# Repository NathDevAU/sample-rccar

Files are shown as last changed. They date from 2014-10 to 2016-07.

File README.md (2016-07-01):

Windows Powered RC Car
===================
---------
Content
-------------

- [Components](#Components)
- [Hooking up Components](#hooking-up-components)
- [Run it!](#run-it!)
- [The Code](#the-code)
- [USB HID Controller Code](#usb-hid-controller-code)
- [Winsock UDP](#winsock-udp)

###Components
- Intel Galileo running Windows off an SD Card
- 5V DC Power Supply (either a wall-powered supply, or a battery pack like [this](http://www.adafruit.com/products/1566) one.)
- A L298N Motor Driver Board ( We've used [this](http://www.ebay.com/itm/like/131207525759?lpid=82) one )
- HID Compliant Controller/Gamepad (We've used an old NES Controller converted to be a HID Device, you can get one [here](http://www.thinkgeek.com/product/1b4c/)
- Microusb Male to USB Female Adapter Cable
- Ethernet Cable
- 4 AA Batteries (or as many batteries as your RC Car needs)
- An RC Car (We've used a Maisito Dune Rover) 
- Male-Female Breadboard Wires

Optional:
- Laptop running Windows & the Remote RC Car Control Application
- Xbox 360 controller for Windows

###Hooking Up Components
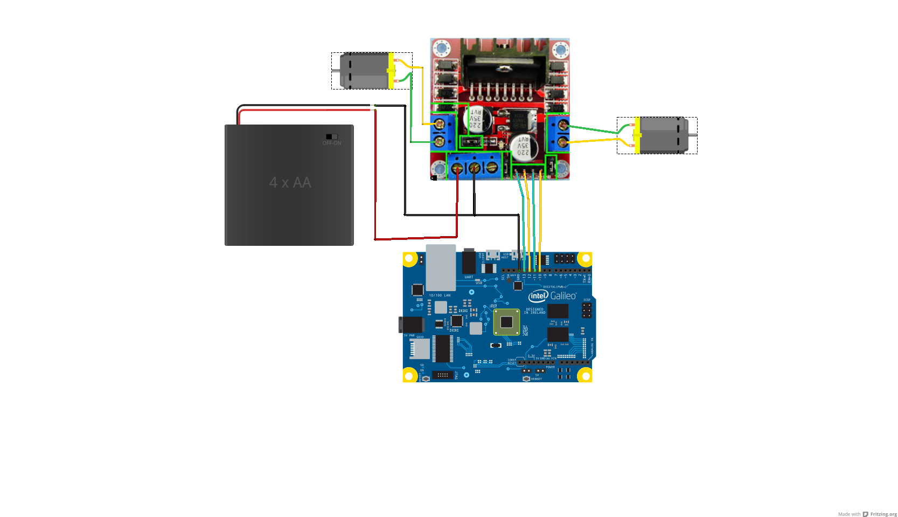
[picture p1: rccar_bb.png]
RC Car


1. Carefully disassemble your purchased RC Car. Specifically, you want to remove the model chassis so you can get at the controller board.

2. You should be able to clearly see 4 wires (two for each motor, assuming a 2 motor RC Car), and 2 more wires from the battery pack, connected to a PCB which contains the controller for the RC Car.

3. Carefully snip away all the leads connected to that PCB. Make sure you know which wire is connected to what part of your RC Car. 

4. Remove the PCB, in it's place, put the L298N Motor Driver Board.

5. Wire up the motor driver board as follows:
>- Connect the +'ve and -'ve leads of one motor to "Output 1" and "Output 2" of the L298N board.
>- Similarily, connect the +'ve and -'ve leads of the other motor to "Output 3" and "Output 4" of the L298N Board.
>- Connect the Battery Pack ground line to the ground input of the L298N Board.
>- Connect the Ground output of the Galileo to the L298N Board Ground input (we want to tie together the grounds of the Galileo and the RC Car)
>- Connect the Battery Pack power line to the +12V input of the L298N Board (don't worry if your battery pack puts out less than 12V)
>- Connect Galileo GPIO pins 13,12,11,10 to Inputs 1-4 of the L298N Board 

**Note: Depending on how you've wired everything up, you may need to play around with the order that you connect these wires to have the controls inverted/regular. In any case, the first motor will be controlled by the inputs 1 and 2, and the second by 3 and 4. To turn on a motor, one of each pair should be high (+5V) and the other low (0V). The motor's direction may be the opposite of what you expect depending on how you've wired it up.

Finally, using the USB adapter cable, plug the NES Controller into the Galileo's USB Host port, and power on the Galileo (make sure the RC Car is turned off until the Galileo is completely booted up and the controller application is running).

###Run it!
Using Visual Studio or Telnet, deploy and run the eCar application. This application runs two threads, one waiting for commands over UDP from a host machine, and the other waiting for local commands from a HID Controller. When commands are received, it drives the GPIO outputs which should drive the motors through the L298N board. 

Once the application has started running on the Galileo, turn on the RC Car and try driving it with the NES controller. With any luck, it should be working just fine! If not, check your wiring as discussed in the Note above.

If you're also using the network-control companion application, you can press "Select" on the NES controller to switch the control mode from local control, to remote from a PC control.

###The Code

There are several files in this project, the purpose of each is listed below.

- Main.cpp
- Controller.cpp and .h
- Communicator.cpp and .h
- Command.h
- nesmapping.h
- stdafx.h

**_Main_**
- The main function that initializes the Galileo pins, and listens to UDP and HID commands to drive the RC Car

**_Controller_**
- Wraps the HID Device communication to talk to the NES Controller

**_Communicator_**
- Wraps the UDP communication done using Winsock

**_Command_**
- An enum representing different commands for the RC Car, used to translate UDP commands

**_nesmapping_**
- Holds the mappings between the NES buttons and their HID identifiers

**_stdafx_**
- Houses all of the external includes for the project

###USB HID Controller Code
Using Windows on Devices gives you access to rich software features that just aren't available on other, similar platforms. One example is full USB support, and several class drivers that are built into the operating system.

For this project, we've used a HID Compliant Gamepad device to drive the input of the RC Car. Take a look at 

**_Controller.h_** and **_Controller.cpp_** to see how to access a HID Device. **_nesmapping.h_** contains the mappings between the HID value and button identifiers with the physical buttons. These need to be determined either from your device's datasheet, or experimentally by writing a program that outputs the button value (see getButtonInput in Controller.cpp for how to read button usages). 

In general, reading from a HID device has XXX main steps, in brackets is the function and line number in which  this step is performed in **_Controller.cpp_**.

1. Get the HID GUID (used by the OS to identify HID devices) [ registerController : 64 ]
2. Get device interface details and iterate through each device until the HID device you're looking for is found. [registerController: 71-93]
3. Create a handle to the HID Device, in the OS this is treated as a file handle [registerController : 94]
4. Get the Preparsed Data for the HID Device, an abstracted data structure that can be used [registerController : 109]
5. Get the Device Capabilities, and from that get the Button and Value Capabilities. These describe the buttons and inputs on the device. For the NES controller, the Values represent the up-down and left-right movement of the DPAD and the Buttons the 4 buttons of the controller. [registerController : 132-141]  
6.  Get an input report by reading from the file [getDpadInput : 213]
7.  Interpret the usage values to get information about the state of the controller [getDpadInput : 234-262]
8.  For button input, repeat steps 6-7 for buttons [getButtonInput]
9. Don't forget to free your allocated data structures.

See MSDN for more documentation, available [here](http://msdn.microsoft.com/en-us/library/windows/hardware/ff538865(v=vs.85).aspx).

###Winsock UDP

With Windows on Devices, it's easy to send simple communications over a network or the internet, using UDP or TCP and the winsock API. For this project, we've used winsock to allow for secondary control over the RC car by UDP packets sent from another computer, anywhere on the network the Galileo is connected to. 

See **_Communicator.h_** and **_Communicator.cpp_** to see how we've used winsock & UDP.

You can also read the documentation on MSDN for more information, available [here](TODO)

===

This project has adopted the [Microsoft Open Source Code of Conduct](http://microsoft.github.io/codeofconduct). For more information see the [Code of Conduct FAQ](http://microsoft.github.io/codeofconduct/faq.md) or contact [opencode@microsoft.com](mailto:opencode@microsoft.com) with any additional questions or comments.

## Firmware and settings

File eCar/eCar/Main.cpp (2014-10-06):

// Copyright(c) Microsoft Open Technologies, Inc. All rights reserved.
// Licensed under the BSD 2 - Clause License.
// See License.txt in the project root for license information.

// Main.cpp : Defines the entry point for the console application.
//


#include "stdafx.h"
#include "arduino.h"
#include "Command.h"
#include "Communicator.h"
#include "Controller.h"
#include "nesmapping.h"


//output pin definitions
#define OUT_UP 10
#define OUT_RIGHT 12
#define OUT_DOWN 11
#define OUT_LEFT 13

Controller * g_controller;
bool * g_dpadValues;
bool * g_buttonValues;
bool g_useNetworkCommands;

Communicator * comm;


int _tmain(int argc, _TCHAR* argv[])
{
	g_useNetworkCommands = false;
    return RunArduinoSketch();
}

void setup()
{   
	//set motor pins to output mode
	pinMode(OUT_UP, OUTPUT);     
	pinMode(OUT_RIGHT, OUTPUT);
	pinMode(OUT_DOWN, OUTPUT);
	pinMode(OUT_LEFT, OUTPUT);

	//set pin outputs to low
	digitalWrite(OUT_UP, LOW);
	digitalWrite(OUT_RIGHT, LOW);
	digitalWrite(OUT_DOWN, LOW);
	digitalWrite(OUT_LEFT, LOW);

	//setup g_controller
	g_controller = new Controller();
	g_controller->registerController(0);
	g_dpadValues = (bool *)malloc(sizeof(int)* 4);
	g_buttonValues = (bool *)malloc(sizeof(int)* 4);

	//setup network communications
	comm = new Communicator();
	comm->startWindowsConnection();
	comm->openUDPSocket();
	comm->setupServerAndBind();
}


// the loop routine runs over and over again forever:
void loop()
{
	if (g_useNetworkCommands)
	{
		switch (comm->receiveCommand())
		{
		case FORWARD:
			digitalWrite(OUT_UP, HIGH);
			digitalWrite(OUT_DOWN, LOW);
			break;
		case RIGHT:
			digitalWrite(OUT_RIGHT, HIGH);
			digitalWrite(OUT_LEFT, LOW);
			break;
		case BACKWARD:
			digitalWrite(OUT_DOWN, HIGH);
			digitalWrite(OUT_UP, LOW);
			break;
		case LEFT:
			digitalWrite(OUT_LEFT, HIGH);
			digitalWrite(OUT_RIGHT, LOW);
			break;
		case STOP_FORWARD:
			digitalWrite(OUT_UP, LOW);
			break;
		case STOP_RIGHT:
			digitalWrite(OUT_RIGHT, LOW);
			break;
		case STOP_BACKWARD:
			digitalWrite(OUT_DOWN, LOW);
			break;
		case STOP_LEFT:
			digitalWrite(OUT_LEFT, LOW);
			break;
		case SWITCH_COMMAND_MODE:
			g_useNetworkCommands = false;
			break;
		default:
			digitalWrite(OUT_UP, LOW);
			digitalWrite(OUT_RIGHT, LOW);
			digitalWrite(OUT_DOWN, LOW);
			digitalWrite(OUT_LEFT, LOW);
		}
	}else
	{
		g_controller->getDPadInput(g_dpadValues);
		g_controller->getButtonInput(g_buttonValues);
		if (g_dpadValues[DPAD_UP_INDEX]){
			digitalWrite(OUT_DOWN, LOW);
			digitalWrite(OUT_UP, HIGH);
		}
		else if (g_dpadValues[DPAD_DOWN_INDEX]){
			digitalWrite(OUT_UP, LOW);
			digitalWrite(OUT_DOWN, HIGH);
		}
		else{
			digitalWrite(OUT_UP, LOW);
			digitalWrite(OUT_DOWN, LOW);
		}

		if (g_dpadValues[DPAD_LEFT_INDEX]){
			digitalWrite(OUT_RIGHT, LOW);
			digitalWrite(OUT_LEFT, HIGH);	
		}
		else if (g_dpadValues[DPAD_RIGHT_INDEX]){
			digitalWrite(OUT_LEFT, LOW);
			digitalWrite(OUT_RIGHT, HIGH);
		}
		else{
			digitalWrite(OUT_LEFT, LOW);
			digitalWrite(OUT_RIGHT, LOW);
		}

		if (g_buttonValues[BUTTON_SELECT_INDEX]){
			g_useNetworkCommands = true;
		}
	}
	
	
}
